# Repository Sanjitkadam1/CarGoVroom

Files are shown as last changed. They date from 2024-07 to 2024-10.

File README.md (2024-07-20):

Engineering materials
====

This repository contains engineering materials of a self-driven vehicle's model participating in the WRO Future Engineers competition in the season 2022.

## Content

* `t-photos` contains 2 photos of the team (an official one and one funny photo with all team members)
* `v-photos` contains 6 photos of the vehicle (from every side, from top and bottom)
* `video` contains the video.md file with the link to a video where driving demonstration exists
* `schemes` contains one or several schematic diagrams in form of JPEG, PNG or PDF of the electromechanical components illustrating all the elements (electronic components and motors) used in the vehicle and how they connect to each other.
* `src` contains code of control software for all components which were programmed to participate in the competition
* `models` is for the files for models used by 3D printers, laser cutting machines and CNC machines to produce the vehicle elements. If there is nothing to add to this location, the directory can be removed.
* `other` is for other files which can be used to understand how to prepare the vehicle for the competition. It may include documentation how to connect to a SBC/SBM and upload files there, datasets, hardware specifications, communication protocols descriptions etc. If there is nothing to add to this location, the directory can be removed.

## Introduction

_This part must be filled by participants with the technical clarifications about the code: which modules the code consists of, how they are related to the electromechanical components of the vehicle, and what is the process to build/compile/upload the code to the vehicle’s controllers._

## How to prepare the repo based on the template

_Remove this section before the first commit to the repository_

1. Clone this repo by using the `git clone` functionality.
2. Remove `.git` directory
3. [Initialize a new public repository on GitHub](https://github.com/new) by following instructions from "create a new repository on the command line" section (appeared after pressing "Create repository" button).

## models 

1. The models named "PART" are files that represent individual parts that have been used and have been joined onto the "Underbody" file to create the "Car Main" to create the Main body of the car 
2. The file named "BackWheel Part" in short is the axle used in the back of the car
3. The files Named "FINAL DESIGN" are individual parts that have been used to assemble the Front Wheel Assembly
4. Note: The lippo Battery Case or Casing has been completely remodeled in the Car Main file iteslf and the individual part has not been updated, which is a trend that can be seen in some of the other parts that have been joined into the "Underbody" file as well since editing it individually in their own respective file locations seemed to be too work intensive

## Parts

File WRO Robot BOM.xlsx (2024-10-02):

Item | Link | Price | Quantity | Total Price
Ball Bearings (20 count) | https://www.amazon.com/dp/B0C75H3GDS | $11.99 | 1 | $11.99
PCBway - Middle rod | Custom Peice | $37.00 | 1 | $37.00
Axle ( 10 count) | https://www.amazon.com/dp/B082ZNLHMN | $8.59 | 1 | $8.59
Lidar Sensor | https://www.amazon.com/youyeetoo-D300-Resistant-Raspberry-Tutorial/dp/B0B1QCV4XR | $77.34 | 1 | $77.34
Fillament (We used 2 different printers) | https://www.amazon.com/Inland-1-75mm-PLA-Printer-Filament/dp/B081S6BMCD?hvadid=692875362841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 | $22.00 | 2 | $44.00
Raspberry Pi 4 Model B | https://www.microcenter.com/product/637834/raspberry-pi-4-model-b | $54.99 | 1 | $54.99
Lipo Battery | https://www.amazon.com/Turnigy-2200mAh-Lipo-Pack-XT60/dp/B07F8KP7FS | $19.99 | 1 | $19.99
Anker Power Bank | https://www.walmart.com/ip/Anker-Power-Bank-10-000mAh-22-5W/5245827263?wmlspartner=wlpa&selectedSellerId=0 | $29.97 | 1 | $29.97
Wheels (4 count) | Donanted by a member, re-used from a different project | $15.00 | 1 | $15.00
82 Teeth Gear | Bought it from a hobby store | $6.99 | 1 | $6.99
55T Motor | https://www.axialadventure.com/product/55t-electric-motor/AXIC2407.html | $23.99 | 1 | $23.99
Buck Convertor (5 count) | https://www.amazon.com/Seloky-Converter-Adjustable-Electronic-Stabilizer/dp/B0DBVYP91F | $8.29 | 1 | $8.29
Soldering wire | https://www.amazon.com/MAIYUM-63-37-Solder-Electrical-Soldering/dp/B075WB98FJ | $1.00 | 1 | $1.00
Cables | https://www.amazon.com/Elegoo-EL-CP-004-Multicolored-Breadboard-arduino/dp/B01EV70C78 | $6.98 | 1 | $6.98
Ultrasonic Sensor (4 count) | https://www.amazon.com/CUQI-Ultrasonic-Measuring-Transmitter-Compatible/dp/B092D2DS1Y | $6.19 | 1 | $6.19

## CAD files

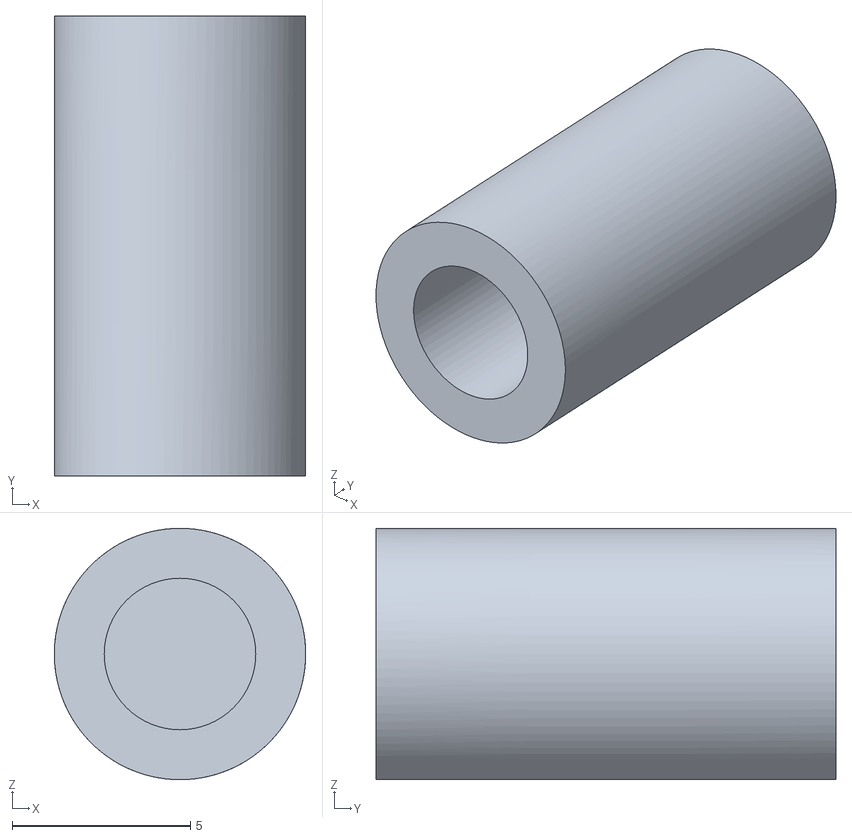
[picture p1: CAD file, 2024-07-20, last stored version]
models/Cap for Front Assembly Holding Pin FINAL DESIGN.stl
7.05 x 12.9 x 7.05

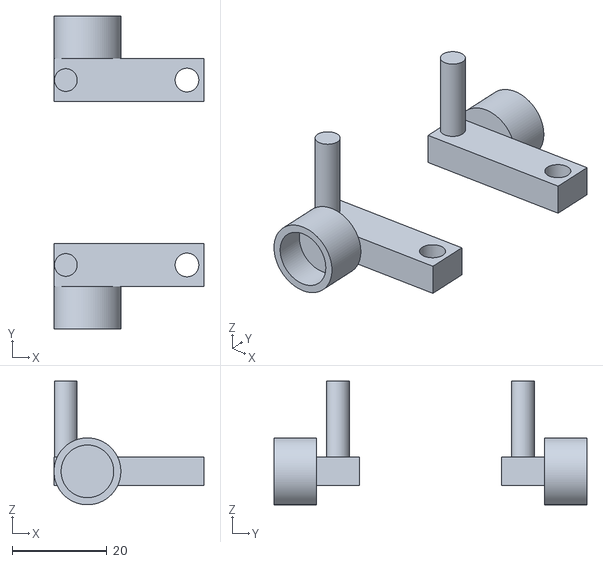
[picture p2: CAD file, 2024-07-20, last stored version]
models/Tyre Holder Front Assembly FINAL DESIGN.stl
31.6 x 66.0 x 26.0

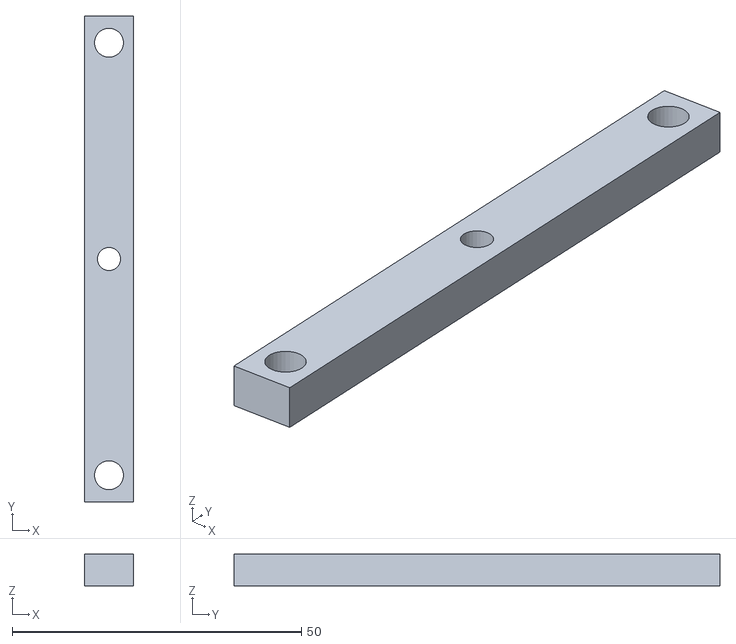
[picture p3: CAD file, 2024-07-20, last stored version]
models/Middle rod Front Assembly FINAL DESIGN.stl
8.50 x 84.0 x 5.50

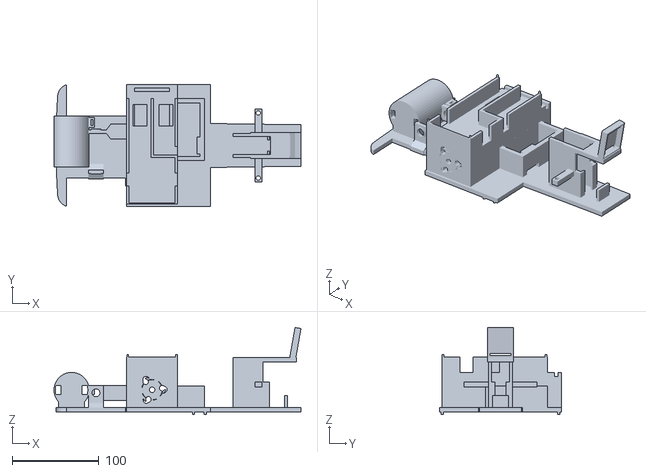
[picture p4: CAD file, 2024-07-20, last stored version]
models/Car Main.stl
284.4 x 140.0 x 100.2

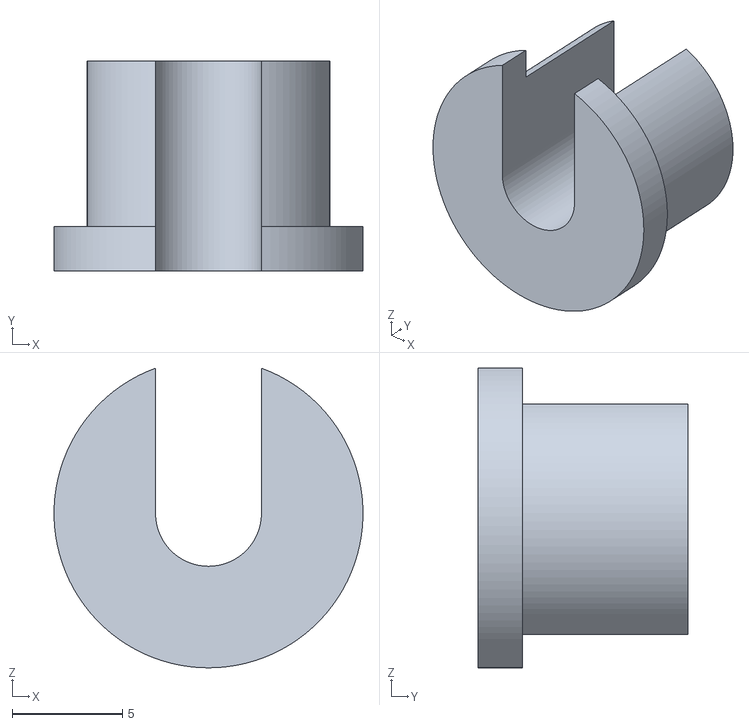
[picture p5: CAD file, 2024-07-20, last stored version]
models/Car Front Assembly spacer FINAL DESIGN.stl
14.0 x 9.50 x 13.6

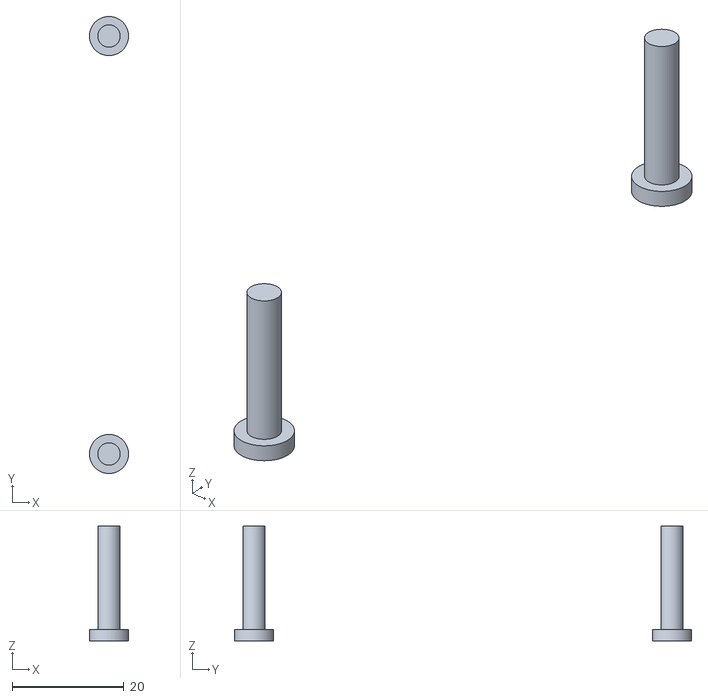
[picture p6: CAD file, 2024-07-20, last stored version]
models/Middle Rod Holding Pins Front Assembly FINAL DESIGN.stl
7.00 x 81.8 x 20.5

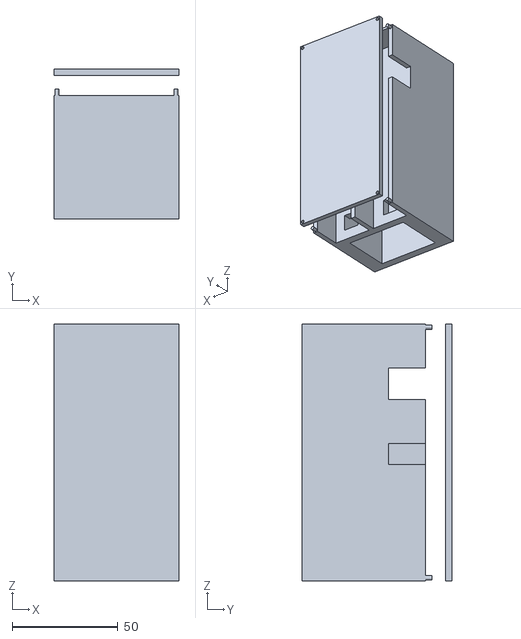
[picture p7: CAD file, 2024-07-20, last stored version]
models/Case for Lippo Battery PART FINAL DESIGN.stl
59.0 x 71.0 x 121.5

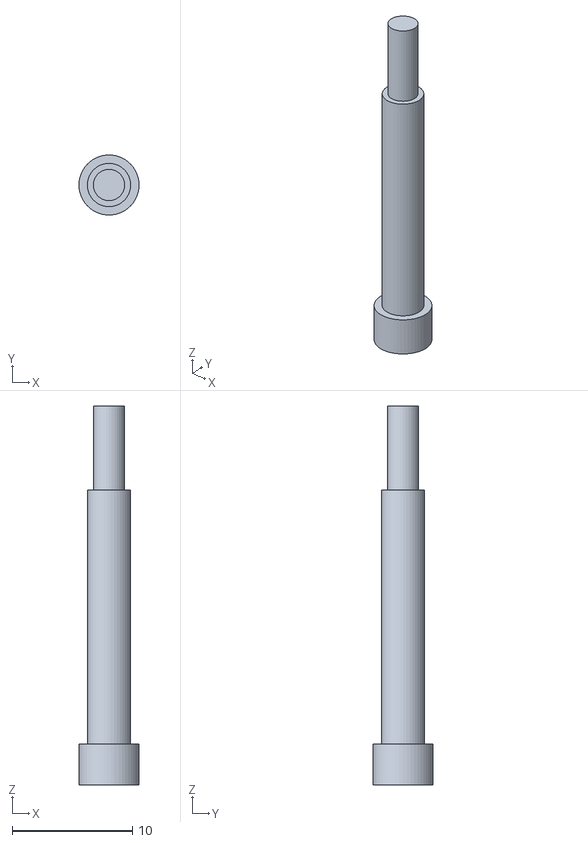
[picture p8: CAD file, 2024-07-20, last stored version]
models/Servo Rod FINAL DESIGN 3.6 mm v7.stl
5.00 x 4.99 x 31.5

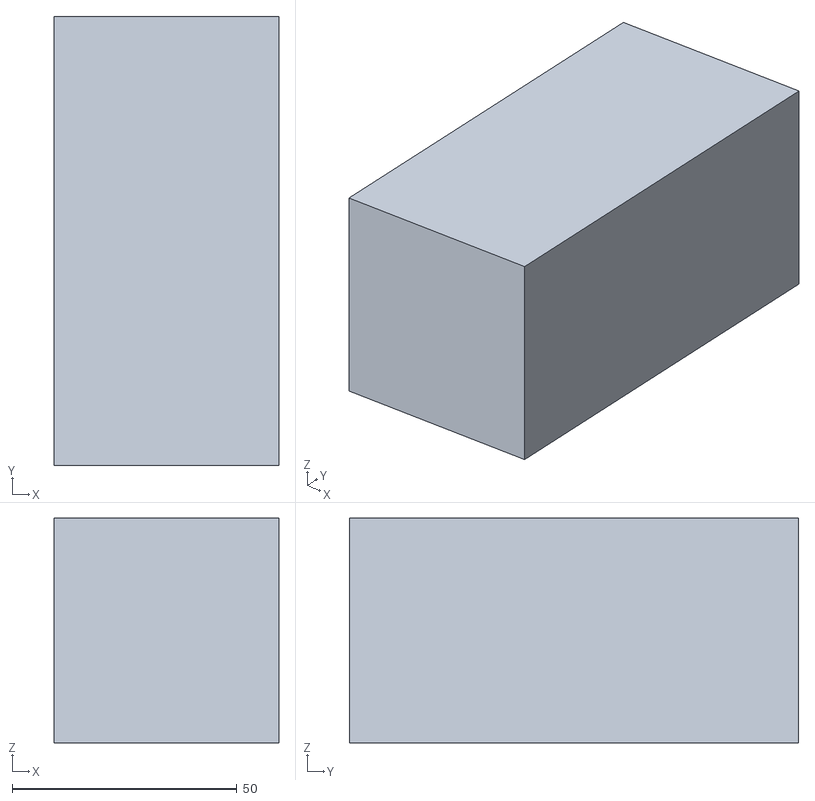
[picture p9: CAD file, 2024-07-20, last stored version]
models/Blocks for WRO FINAL DESIGN.stl
50.0 x 100.0 x 50.0

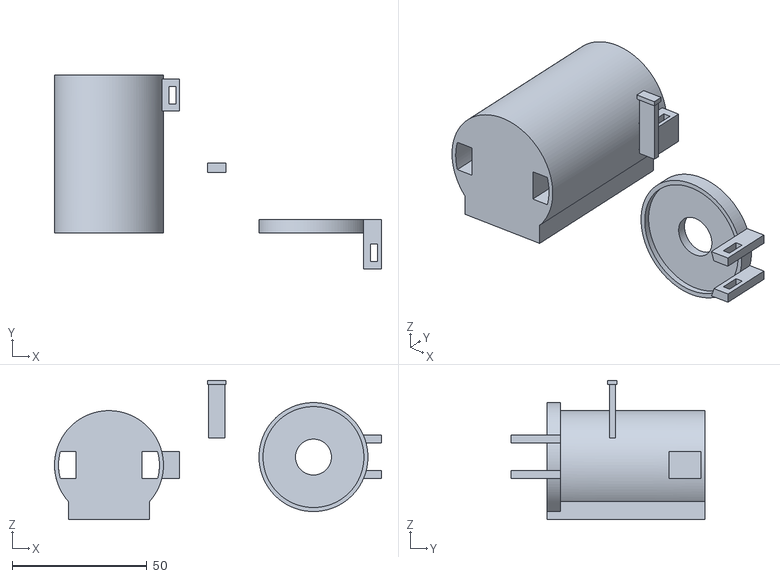
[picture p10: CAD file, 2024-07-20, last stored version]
models/Casing for Motor PART FINAL DESIGN.stl
121.5 x 72.2 x 51.8

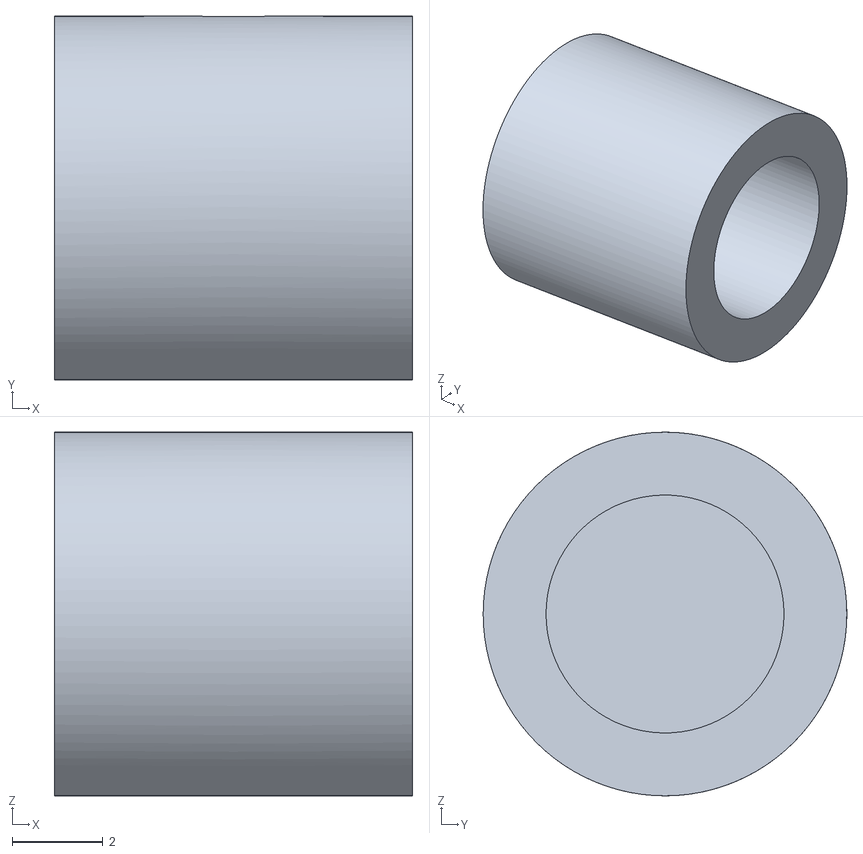
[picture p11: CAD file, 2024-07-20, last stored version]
models/Cap for Bearing Front Wheel Section FINAL DESIGN.stl
7.90 x 8.03 x 8.02

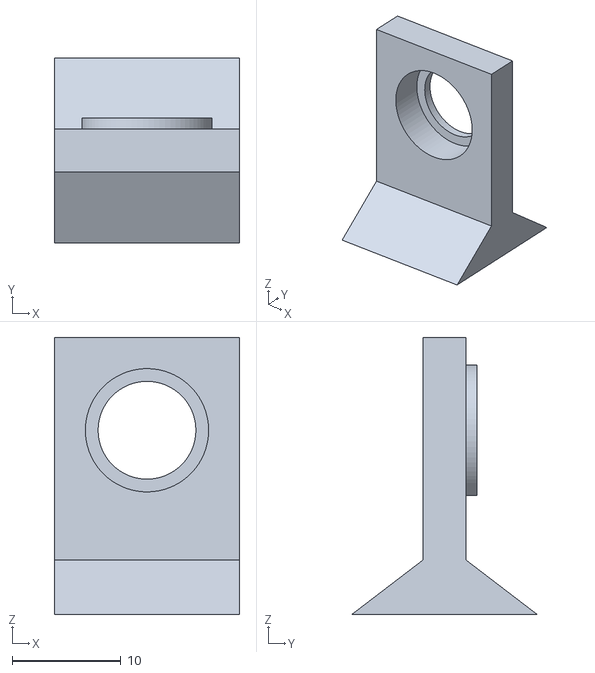
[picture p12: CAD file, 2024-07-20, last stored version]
models/Underbody Holder PART.stl
17.1 x 17.1 x 25.5

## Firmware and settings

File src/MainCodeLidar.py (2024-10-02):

import time as t
import os
os.system ("sudo pigpiod")
print("importing packages...")
t.sleep(1)
import pigpio # type: ignore
import pigpio # type: ignore
import RPi.GPIO as PIN # type: ignore
import numpy as np # type: ignore
import cv2 as cv # type: ignore
from picamera2 import Picamera2 # type: ignore
import matplotlib.pyplot as plt # type: ignore
import matplotlib.pyplot as plt # type: ignore
import time 
import smbus # type: ignore
import math
import subprocess
import serial
print("Imported all nessesary packages")

port = "/dev/serial0"
baud_rate = 230400

ser = serial.Serial(port=port, baudrate=baud_rate, parity="N")

#	General init
print("Initialization Starting...")
t.sleep(0.5)
START = t.time()
#track = object.track()

#	Motor init
pi = pigpio.pi()
esc = 18
pi.set_servo_pulsewidth(esc, 0)

#	Servo init
print("Servo Calibrating...")
servo = 14 #GPIO: 14, Pin: 8
print("Servo Calibration Complete") 

# Camera init
print("Camera Calibrating...")
picam = Picamera2()
config = picam.create_still_configuration()
picam.configure(config)
picam.start()
t.sleep(2)
print("Camera Calibration Complete")

print("Initialization Complete")
t.sleep(1)


def graph(angRet, lenRet): # Polar coordinates -> Cartesian (and graphs)
    angRet = np.array(angRet)

    ang_rad = np.deg2rad(angRet)

    x = np.cos(ang_rad)*lenRet
    y = np.sin(ang_rad)*lenRet

    ax = plt.scatter(x, y)
    plt.show()

def toCart(angRet, lenRet): # Polar coordinates -> Cartesian
    angRet = np.array(angRet)
    ang_rad = np.deg2rad(angRet)

    x = np.cos(ang_rad)*lenRet
    y = np.sin(ang_rad)*lenRet

    return x, y

def position(ang, lens): # Returns x, y, theta -> Cars current position
    offcenter = getAngle(ang, lens) 
    ang = np.array(ang)
    for i in range(0, len(ang)):
        if (ang[i]<offcenter):
            ang[i] = ang[i] - offcenter+360
        else:
            ang[i] = ang[i] - offcenter
    x, y = toCart(ang, lens)
    left = []
    right = []
    for i in range(0, len(x)):
        if y[i] > 0:
            if -250 < x[i] < 250:
                left.append(y[i])
        else:
            if -250 < x[i] < 250:
                right.append(y[i])
    xl = np.median(left)
    print("xl: ", xl)
    xr = -(np.median(right))
    print("xr: ", xr)
    front = []
    back = []
    for i in range(0, len(y)):
        if x[i] > 0:
            if -(0.5*xr) < y[i] < 0.5*xl:
                front.append(x[i])
        else:
            if -(0.5*xr) < y[i] < 0.5*xl:
                back.append(x[i])
    yf = np.median(front)
    print("yf: ", yf)
    if len(back) == 0:
        print("unreliable y (back missing)")
        yb = 3000 - (yf+diam)
    else: 
        yb = -(np.median(back))
    print("yb: ", yb)

    diam = 35.1

    leny = yb + yf + diam
    lenx = xr + xl + diam

    if not (2950 > leny) and (3050 < leny):
        print("unreliable y")
    if not ((950 > lenx) and (1050 < lenx)) or ((2950 > lenx) and (3050 < lenx)):
        print("unreliable x")

    return (xl, yb, offcenter)

def getAngle(ang, lens): # Get the angle 
    x = []
    y = []
    xi, yi = toCart(ang, lens)
    for i in range(0, len(yi)):
        if yi[i] > 0:
            if -150 < xi[i] < 150:
                x.append(xi[i])
                y.append(yi[i])
    n = len(x)
    x = np.array([x])
    y = np.array([y])

    # Calculate the components of the linear regression equation
    sum_x = np.sum(x)
    sum_y = np.sum(y)
    sum_x_sq = np.sum(x**2)
    sum_xy = np.sum(x * y)

    # Use the linear regression formula
    if (n * sum_x_sq - sum_x**2) != 0:  # Avoid division by zero
        m = (n * sum_xy - sum_x * sum_y) / (n * sum_x_sq - sum_x**2)
    else:
        m = 0  # Special case where the regression isn't possible

    # Now we calculate the angle from the regression slope
    if m != 0:
        rad = np.arctan(m)  # arctan of the slope gives the angle in radians
        deg = np.degrees(rad)  # Convert radians to degrees
    else:
        deg = 0  # If no slope, angle is 0

    print("Computed angle (deg):", deg)

    return deg

def readData(): # Reads tbe data coming from the LIDAR thru the UART hardware port. (Custom device driver for the LIDAR)
    while True:
        data = ser.read(1)
        if data:
            if data[0] == 0x54:
                break

    packet = b''
    while True:
        data = ser.read(1)
        if data:
            packet = packet + data
            if data[0] == 0x54:
                break

    if not len(packet) > 46:
        return readData()

    if not (packet[0] == 0x2C):
        print("Woah", hex(packet[0]))
        return readData()
 
    Speed = int.from_bytes(packet[1:3], byteorder="little")
    startAngle = int.from_bytes(packet[3:5], byteorder="little")
    measure = packet[5:len(packet)-5]
    postdata = packet[len(packet)-5:]

    lengths = []
    intens = []
    for i in range(0, len(measure)//3):
        lengths.append(int.from_bytes(measure[(3*i):(3*i)+2], byteorder="little"))
        intens.append(int.from_bytes(measure[(3*i)+2:(3*i)+3]))


    endAngle = int.from_bytes(postdata[0:2])
    startAngle = startAngle/100
    endAngle = endAngle/100
    
    if (startAngle > 360) or (endAngle > 360):
        return readData()
    
    if (startAngle > endAngle):
        step = endAngle+360 - startAngle
    else:
        step = (endAngle-startAngle)/(len(lengths)-1)
    angles = []
    for i in range(0, len(lengths)):
        ang = startAngle + (step*i)
        if ang>360:
            ang = ang - 360
        angles.append(ang)
    
    return angles, lengths

def getData(): # Reads data in a loop and compiles it
	angRet = []
	lenRet = []
	for _ in range(0, 30):
		ang, lens = readData()
		for i in range(0, len(ang)):
			angRet = np.concatenate((angRet, np.array(ang)))
			lenRet = np.concatenate((lenRet, np.array(lens)))
    
	return angRet, lenRet

def Bservo(x): # Controls the servo. We found the relationship between PWM and the servo 
    servo = 14
    if x > 30:
        pi.set_servo_pulsewidth(servo, (6.5*30) + 1550)
        return
    elif x < -30:
        pi.set_servo_pulsewidth(servo, (6.5*-30) +1550)
        return
    pulsewidth = (6.5*x) + 1550
    pi.set_servo_pulsewidth(servo, pulsewidth)
    return

# This was code to graph the entire map and was used in the testing

# fig, ax = plt.subplots()
# innerbox = ([1000,2000,2000,1000,1000],[1000,1000,2000,2000,1000])
# ax.plot(innerbox, label = "innerbox", color = 'black')
# outerbox = ([0,3000,3000,0,0],[0,0,3000,3000,0])
# ax.plot(outerbox, label = "outerbox", color = 'black')

def detectObjs(): # Detects objects (OpenCV). We were trying to set up an A* but ran out of time...
    picam.capture_file("test.jpeg")
    img = cv.imread("test.jpeg")
    height, width, channels = img.shape
    hsvimg = cv.cvtColor(img, cv.COLOR_BGR2HSV)
    side = ""

    #Finding green 
    greenLow = np.array([51, 100, 100])
    greenHigh = np.array([61, 255, 255])
    greenMask = cv.inRange(hsvimg, greenLow, greenHigh)

    greenContours, greenHierarchy = cv.findContours(greenMask, cv.RETR_TREE, cv.CHAIN_APPROX_SIMPLE)
    minarea = 500
    for contour in greenContours:
        MAX = -1
        x, y, Cwidth, Cheight = cv.boudingRect(contour)
        if Cheight > height/10 and (Cwidth*Cheight) > MAX and Cwidth > width/10:
            MAX = Cheight*Cwidth
            if (x > width/2 and (x-Cwidth) > width/2) and (MAX > minArea):
                sideg = "left"
            elif x < width/2: 
                sideg = "right"
            else:
                sideg = "none"
        else:
            sideg = "none"

	# if (side == "left"):
	# 	objGreen = object.obj(turn, num, "green")
	# 	track.add(objGreen)
	# elif (side == "right"):
	# 	objGreen = object.obj(turn, num+1, "green")
	# 	track.add(objGreen)

	#Finding red
    lower_red1 = np.array([0, 100, 100])
    upper_red1 = np.array([10, 255, 255])
    lower_red2 = np.array([170, 100, 100])
    upper_red2 = np.array([180, 255, 255])

    redmask1 = cv.inRange(img, lower_red1, upper_red1)
    redmask2 = cv.inRange(img, lower_red2, upper_red2)
    redMask = cv.bitwise_or(redmask1, redmask2)

    redContours, redHierarchy = cv.findContours(redMask, cv.RETR_TREE, cv.CHAIN_APPROX_SIMPLE)
    side = None
    for contour in redContours:
        MAX = -1
        x, y, Cwidth, Cheight = cv.boudingRect(contour)
        if Cheight > height/10 and (Cwidth*Cheight) > MAX and Cwidth > width/10:
            MAX = Cheight*Cwidth
            if (x > width/2 and (x-Cwidth) > width/2) and (MAX > minArea):
                sider = "left"
            elif x < width/2: 
                sider = "right"
            else:
                sider = "none"
        else:
            sider = "none"
	
	# if (objGreen.turn == "left" and not side == None):
	# 	print("ERROR DUPLICATE OBJECT DETECTED OR BINARY ERROR")

	# if (side == "left"):
	# 	objRed = object.obj.__init__(turn, num, "red")
	# 	track.add(objRed)
	# elif (side == "right"):
	# 	if (objGreen.turn == "right"):
	# 		print("ERROR DUPLICATE OBJECT DETECTED")
	# 	objRed = object.obj.__init__(turn, num+1, "red")
	# 	track.add(objRed)

	# return turn, num

    if sideg == "left": # If the left is green the right cannot be red
        return sideg
    elif sideg == "right": # If the right is green then center will always be true. (The case of left green is resolved above) 
        return "center"
    else: # No green
        if sider == "right": # If red is right, only right will be true.
            return "right"
        else:
            return "center" # If red is on the left or there are no objects only center can be true.

def reedsShep(current, final): # This runs a bash script to trigger a Reeds Shepp simulation in a virtual environment that runs an older version of python.
    # Run the bash script and capture the output
    result = subprocess.run(['bash', 'movement.sh'], capture_output=True, text=True, input=(current[0], current[1], current[2], final[0], final[1], final[2]))

    # The output will be captured in result.stdout
    print("Script Output:")
    print(result.stdout)

    # If there is any error, it will be in result.stderr
    if result.stderr:
        print("Script Error:")
        print(result.stderr)
        return 0
    return result.stdout()

def stop(): # Stops the car. (Our motor is really bad)
    esc = 18
    pi.set_servo_pulsewidth(esc, 1500)
    t.sleep(0.01)
    pi.set_servo_pulsewidth(esc, 1300)
    t.sleep(0.01)
    pi.set_servo_pulsewidth(esc, 1500)
    t.sleep(0.01)
    pi.set_servo_pulsewidth(esc, 1300)
    t.sleep(0.01)
    pi.set_servo_pulsewidth(esc, 1500)

def start(): # Starts at 1600 PWM
    esc = 18
    pi.set_servo_pulsewidth(esc, 1500)
    pi.set_servo_pulsewidth(esc, 1600)

def back(): #Starts going back
    esc = 18
    stop()
    pi.set_servo_pulsewdith(esc, 1300)
    t.sleep(0.2) # Edit this
    pi.set_servo_pulsewdith(esc, 1500)
    pi.set_servo_pulsewidth(esc, 1600)
    pi.set_servo_pulsewdith(esc, 1500)
    pi.set_servo_pulsewdith(esc, 1600)
    t.sleep(0.01)
    pi.set_servo_pulsewdith(esc, 1500)

def checkpos(current, final): # Compares two points of form (x, y, theta) with a adjustable tolerance
    tolerance = 10
    checkx = np.abs(final[0] - current[0]) < tolerance
    checky = np.abs(final[1] - current[1]) < tolerance
    
    print("Position checks", checkx, checky)
    return checkx and checky

def goto(final): # Compiles a lot of functions above to go to a point of form (x, y, theta) where x and y are relative to the turn and theta is the offset angle of the car from the wall
    tolerance = 10 #car should stop minimum of 10mm ahead of the point, adjustable 
    angRet, lenRet = getData() #gets data from LIDAR
    current = position(angRet,lenRet) #gets current position from data from LIDAR
    ang = getAngle() #gets cars current position
    rs = reedsShep(current,final) #reedsShep() function will give a list of points(tuples), in the format of (x,y,velocity)
    for i in range(0,rs.length()): #for each tuple in rs
        point = rs[i] #the final point for this loop is point
        angRet, lenRet = getData()
        current = position(angRet, lenRet) #gets current pos
        angL = math.atan((point[1] - current[1])/(point[0] - current[0])) # gets the angle of the line from current pos to point
        angL = angL*180/np.pi #converts rad to deg 
        Bservo(angL - ang) #sets the angle to the difference between the angle of the line, and the angle of the current pos
        if point[2] < 0: #if velocity is negative, the car needs to move backwards
            back() #starts moving the car backwards
        else:
            start() #starts moving the car forwards
        check = checkpos()
        while check != True: #until the car gets to point 
            angRet, angLet = getData()
            current = position(angRet, angLet) #gets current pos
            ang = getAngle(angRet, angLet) #gets current angle
            
            if ang < angL or ang > angL:
                Bservo(angL - ang) #sets the angle to the difference between the angle of the line, and the angle of the current pos
            check = checkpos()
        stop() #stops the car
    stop()
    angRet, lenRet = getData() #gets data from LIDAR
    current = position(angRet,lenRet) #gets current position from data from LIDAR
    if not checkpos(current, final):
        print("not there just yet, retrying")
        goto(final)
    else:
        print("reached", final)

def objResponse(turn, num): # Returns the appropriate response for the detect objects
    if num == 0:
        y = 1100
    elif num == 1:
        y = 1600
    elif num == 2:
        y = 2100
    
    if turn == "center":
        x = 500
    elif turn == "left":
        x = 190
    elif turn == "right":
        x = 690
    
    return (x, y, 0)

for _ in range(0, 3):
    for _ in range(0, 4):
        center = 500
        pos = [960, 1460, 1960]
        for i in range(0, 3):
            goto(center, pos[i], 0)
            final = objResponse(detectObjs(), 0)
            goto(final)

# Parrelel parking and reverse was not implemented

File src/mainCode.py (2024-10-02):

#-------------------------Packages--------------------------#
import time as t
import os
os.system ("sudo pigpiod")
print("importing packages...")
t.sleep(1)
import pigpio # type: ignore
import pigpio # type: ignore
import RPi.GPIO as PIN # type: ignore
import numpy as np # type: ignore
import cv2 as cv # type: ignore
from picamera2 import Picamera2 # type: ignore
import matplotlib.pyplot as plt # type: ignore
import matplotlib.pyplot as plt # type: ignore
import time 
import smbus # type: ignore
print("Imported all nessesary packages")

#-------------------------Init Code-------------------------#
#	General init
print("Initialization Starting...")
t.sleep(0.5)
START = t.time()
track = object.track()

#	Motor init
pi = pigpio.pi()
esc = 18
pi.set_servo_pulsewidth(esc, 0)

#	Servo init
print("Servo Calibrating...")
Bservo = 14 #GPIO: 14, Pin: 8
print("Servo Calibration Complete")

# Camera init
print("Camera Calibrating...")
picam = Picamera2()
config = picam.create_still_configuration()
picam.configure(config)
picam.start()
t.sleep(2)
print("Camera Calibration Complete")

print("Initialization Complete")
t.sleep(1)
#-------------------------Functions-------------------------#

def detectObjs(track, turn):
	picam.capture_file("test.jpeg")
	img = cv.imread("test.jpeg")
	height, width, channels = img.shape
	hsvimg = cv.cvtColor(img, cv.COLOR_BGR2HSV)

	#Finding green 
	greenLow = np.array([51, 100, 100])
	greenHigh = np.array([61, 255, 255])
	greenMask = cv.inRange(hsvimg, greenLow, greenHigh)

	greenContours, greenHierarchy = cv.findContours(greenMask, cv.RETR_TREE, cv.CHAIN_APPROX_SIMPLE)
	side = None
	for contour in greenContours:
		MAX = -1
		x, y, Cwidth, Cheight = cv.boudingRect(contour)
		if Cheight > height/10 and (Cwidth*Cheight) > MAX and Cwidth > width/10:
			MAX = Cheight*Cwidth
			if (MAX > minArea):
				if (x > width/2 and (x-Cwidth) > width/2):
					side = "left"
				elif x < width/2: 
					side = "right"

	if (side == "left"):
		objGreen = object.obj(turn, num, "green")
		track.add(objGreen)
	elif (side == "right"):
		objGreen = object.obj(turn, num+1, "green")
		track.add(objGreen)

	#Finding red
	lower_red1 = np.array([0, 100, 100])
	upper_red1 = np.array([10, 255, 255])
	lower_red2 = np.array([170, 100, 100])
	upper_red2 = np.array([180, 255, 255])

	redmask1 = cv.inRange(img, lower_red1, upper_red1)
	redmask2 = cv.inRange(img, lower_red2, upper_red2)
	redMask = cv.bitwise_or(redmask1, redmask2)

	redContours, redHierarchy = cv.findContours(redMask, cv.RETR_TREE, cv.CHAIN_APPROX_SIMPLE)
	side = None
	for contour in redContours:
		MAX = -1
		x, y, Cwidth, Cheight = cv.boudingRect(contour)
		if Cheight > height/10 and (Cwidth*Cheight) > MAX and Cwidth > width/10:
			MAX = Cheight*Cwidth
			minArea = 0 # !!!! SET THIS V. IMP
			if (MAX > minArea):
				if (x > width/2 and (x-Cwidth) > width/2):
					side = "left"
				elif x < width/2: 
					side = "right"
	
	if (objGreen.turn == "left" and not side == None):
		print("ERROR DUPLICATE OBJECT DETECTED OR BINARY ERROR")

	if (side == "left"):
		objRed = object.obj.__init__(turn, num, "red")
		track.add(objRed)
	elif (side == "right"):
		if (objGreen.turn == "right"):
			print("ERROR DUPLICATE OBJECT DETECTED")
		objRed = object.obj.__init__(turn, num+1, "red")
		track.add(objRed)

	return turn, num


def Bservo(x): #function to turn the servo
	servo = 14 #GPIO: 14, Pin: 8 
	if x > 40 or x < -40: #our wheels cant turn more than 40 degrees both ways.
		return Exception
	pulse_width = (6.5*x) + 1550 #equation we have made for pulsewidth conversion. y(pulsewidth) = 6.5(amount changing per degree)*x(degrees) + 1550(center)
	pi.set_servo_pulsewidth(servo, pulse_width)

# needs to made
def turn90(side):
	turnRadius = 0
	PI = 22/7
	Bservo(40)
	go(0.5*PI*turnRadius) # change this later when you know the turn radius

# works
def gyroVals(): 
	rawDataX = sm.read_i2c_block_data(0x68, 0x43, 2) #reads the data from X, Y, and Z channels of the gyro
	rawDataY = sm.read_i2c_block_data(0x68, 0x45, 2)
	rawDataZ = sm.read_i2c_block_data(0x68, 0x47, 2)
	
	rawX = (rawDataX[0] << 8) | rawDataX[1] #ask sol
	rawY = (rawDataY[0] << 8) | rawDataY[1]
	rawZ = (rawDataZ[0] << 8) | rawDataZ[1]

	# 16 bit negative (?)
	if rawX > 32767:
		rawX -= 65536
	if rawY > 32767:
		rawY -= 65536
	if rawZ > 32767:
		rawZ -= 65536

	gyroX = rawX-gyroCalibX #returning values
	gyroZ = rawZ-gyroCalibZ
	gyroY = rawY-gyroCalibY
		
	
	return gyroX, gyroY, gyroZ

# works
def accelVals (): 
	rawDataX = sm.read_i2c_block_data(0x68, 0x3B, 2) #reads the data from X, Y, and Z channels of the Accelerometer
	rawDataY = sm.read_i2c_block_data(0x68, 0x3D, 2)
	rawDataZ = sm.read_i2c_block_data(0x68, 0x3F, 2)

	rawX = (rawDataX[0] << 8) | rawDataX[1] #ask sol
	rawY = (rawDataY[0] << 8) | rawDataY[1]
	rawZ = (rawDataZ[0] << 8) | rawDataZ[1]

	# 16 bit negative 
	if rawX > 32767:
		rawX -= 65536
	if rawY > 32767:
		rawY -= 65536
	if rawZ > 32767:
		rawZ -= 65536

	accelX = rawX-accelCalibX #returning values
	accelY = rawY-accelCalibY
	accelZ = rawZ-accelCalibZ



	return accelX, accelY, accelZ

# Get from the pi
def goStraight(distance):
		esc = 20
		# goes ahead roughly 12 cm at 1600 for 0.25sec goes behind roughly 7.25 cm at 1300 for 0.25sec
		initd = depth(0)
		error = 2
		if (distance>0):
			pi.set_servo_pulsewidth(esc, 1500)
			time.sleep(0.001)
			i = distance/12
			rem = distance%12
			for q in range(0, i):
				pi.set_servo_pulsewidth(esc, 1600)
				time.sleep(0.25)
				pi.set_servo_pulsewidth(esc, 0)
				time.sleep(0.1)
			pi.set_servo_pulsewidth(esc, 1600)
			time.sleep((rem/12)*0.25)
			pi.set_servo_pulsewidth(0)
			finald = depth(0)
			offby = finald - initd
			if ((distance - offby.__abs__).__abs__ > error):
				goStraight(offby)
		else:
			pi.set_servo_pulsewidth(esc, 1500)
			time.sleep(0.001)
			pi.set_servo_pulsewidth(esc, 1300)
			time.sleep(0.001)
			pi.set_servo_pulsewidth(esc, 1500)
			i = distance/7.25
			rem = distance%7.25
			for q in range(0, i):
				pi.set_servo_pulsewidth(esc, 1300)
				time.sleep(0.25)
				pi.set_servo_pulsewidth(esc, 0)
				time.sleep(0.1)
			pi.set_servo_pulsewidth(esc, 1300)
			time.sleep((rem/12)*0.25)
			pi.set_servo_pulsewidth(0)
			finald = depth(0)
			offby = finald - initd
			if ((distance - offby.__abs__).__abs__ > 2):
				goStraight(offby)

# Needs to be made
def go(distance):
	print("Sol you dipshit do this")

# Needs to be made
def center():
	error = 3
	while True:
		left = depth(1, 0)
		right = depth(2, 0)
		error = 2
		left = depth(1)
		right = depth(2)
		if right == left:
			return None
		elif right > left:
			if right < (left+error):
				return None
			else:
				dist = right-left
				shiftCar(dist/2, "right", 30)
		else:
			if (right+error > left):
				return None
			else:
				dist = left-right
				shiftCar(dist/2, "left", 30)
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

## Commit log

2024-07-07 Added gyrotest and serialsender
2024-07-10 Implemented turn90, Bservo, and added Motor
2024-07-10 Added Prints for possible debugging, Mini servo init, camera init and takephoto function
2024-07-14 pin change
2024-07-14 HealthCheck added. mainCode changes, motorConfig changes
2024-07-18 Servo Values retuned
2024-07-20 bugfix - depth sensor GPIO values
    [SPEED.py, healthCheck.py, mainCode.py]
2024-07-20 bugfix - object detection ahead
    [mainCode.py]
2024-07-20 Add files via upload
    These STL files are the CAD files that we CADed using Fusion 360 for the Car, the files labeled as "PART" mean that they are individual components that have been joined into the underbody to create t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
    [Blocks for WRO FINAL DESIGN.stl, Cap for Bearing Front Wheel Section FINAL DESIGN.stl, Cap for Front Assembly Holding Pin FINAL DESIGN.stl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]
2024-09-14 Servo control stuff
2024-09-17 Added Motor Control-our
2024-09-26 added lidar device driver
2024-09-27 added methods to LIDAR.p
2024-09-27 added to LIDAR.py
2024-09-27 Trying to fix the lidar 360
2024-09-28 Update MotorControl-ext.py
    Changed ESC Value
2024-09-28 Changed esc GPIO #, changed irrelenvant comment
2024-09-28 Added lidar graphing method using matplotlib
2024-09-28 removed extraneous lidar.py, updated the lidar.py that is in calibcode
2024-09-28 Fixed Lidar code
2024-10-01 fixed goto(), removing track object, purged models folder
    [Blocks for WRO FINAL DESIGN.stl, Cap for Bearing Front Wheel Section FINAL DESIGN.stl, Cap for Front Assembly Holding Pin FINAL DESIGN.stl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]
2024-10-01 Create (BOM) Bill Of Materials
    Contains all of the items that we have purchased in order to build the robot.
2024-10-01 Rename CamScanner 09-30-2024 21.59.pdf to Electrical Wiring Diagram
2024-10-02 Rename WRO Robot BOM (2).xlsx to WRO Robot BOM.xlsx
    [WRO Robot BOM.xlsx]
